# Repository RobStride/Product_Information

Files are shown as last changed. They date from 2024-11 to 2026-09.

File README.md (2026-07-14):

# RobStride 产品资料 / Product Information

北京灵足时代科技有限公司（RobStride Dynamics Co., Ltd）RS 系列一体化高性能关节模组产品资料。

- 产品规格文档：[灵足时代 RS 系列产品规格介绍（260713）](./灵足时代RS系列产品规格介绍(260713）.pdf)
- 中文资料：[产品资料](./产品资料)
- English literature: [Product Literature](./Product%20Literature)
- 官网 / Website: [www.robstride.com](https://www.robstride.com)

> 以下参数整理自 2026-07-13 版产品规格文档。额定扭矩需配合文档注明的铝制散热板条件使用；完整尺寸、性能曲线及过载曲线请查看原 PDF。

## 产品选型 / Product Selection

| 型号 Model | 产品类型 Product | 价格 Price | 额定扭矩 Rated Torque | 峰值扭矩 Peak Torque | 额定电压 Rated Voltage | 电压范围 Voltage Range | 空载转速 No-load Speed | 重量 Weight | 减速比 Ratio | 磁编码器 Encoders |
| --- | --- | ---: | ---: | ---: | ---: | ---: | ---: | ---: | ---: | ---: |
| RS00 | 14 N·m 一体化准直驱关节模组 / Integrated QDD Actuator | ¥598 | 5 N·m @ 100 rpm | 14 N·m | 48 V | 24–60 V | 315 rpm ±10% | 310 g ±3 g | 10:1 | 2 |
| RS01 | 17 N·m 一体化准直驱关节模组 / Integrated QDD Actuator | ¥599 | 7 N·m @ 100 rpm | 17 N·m | 36 V | 24–48 V | 315 rpm ±10% | 380 g ±3 g | 7.75:1 | 1 |
| RS02 | 17 N·m 一体化准直驱关节模组 / Integrated QDD Actuator | ¥699 | 7 N·m @ 100 rpm | 17 N·m | 48 V | 24–60 V | 410 rpm ±10% | 380 g ±3 g | 7.75:1 | 2 |
| RS02-IP67 | 17 N·m IP67 一体化准直驱关节模组 / IP67 Integrated QDD Actuator | ¥999 | 7 N·m @ 100 rpm | 17 N·m | 48 V | 24–60 V | 410 rpm ±10% | 490 g | 7.75:1 | 2 |
| RS03 | 60 N·m 一体化准直驱关节模组 / Integrated QDD Actuator | ¥999 | 21 N·m @ 100 rpm | 60 N·m | 48 V | 15–60 V | 195 rpm ±10% | 900 g ±20 g | 9:1 | 2 |
| RS04 | 120 N·m 一体化准直驱关节模组 / Integrated QDD Actuator | ¥1199 | 40 N·m / 35 N·m @ 50 rpm¹ | 120 N·m | 48 V | 15–60 V | 200 rpm ±10% | 1420 g ±20 g | 9:1 | 2 |
| RS05 | 5.5 N·m 一体化准直驱关节模组 / Integrated QDD Actuator | ¥499 | 1.8 N·m @ 100 rpm | 5.5 N·m | 48 V | 15–60 V | 480 rpm ±10% | 191 g | 7.75:1 | 2 |
| RS06 | 36 N·m 一体化准直驱关节模组 / Integrated QDD Actuator | ¥849 | 11 N·m @ 100 rpm | 36 N·m | 48 V | 15–60 V | 480 rpm ±10% | 621 g | 9:1 | 2 |

¹ RS04 使用 345 mm × 345 mm 铝制散热板时额定扭矩为 40 N·m；使用 220 mm × 200 mm 铝制散热板时为 35 N·m。

## 通用特性 / Common Specifications

- 驱动方式 / Drive method：FOC
- 相数 / Phases：3
- 运转方向 / Running direction：CW/CCW
- 使用温度 / Operating temperature：-20–50 ℃
- 使用湿度 / Operating humidity：5–85%
- 保存温度 / Storage temperature：-30–70 ℃
- 绝缘等级 / Insulation class：Class B
- 齿轮工艺 / Gear material：机加工钢 / Machined steel

## 使用说明书 / User Manuals

| 型号 Model | 中文说明书 | English Manual | 3D 模型 |
| --- | --- | --- | --- |
| RS00 | [RS00 使用说明书 260713](./产品资料/RS00/RS00使用说明书260713.pdf) | [RS00 User Manual](./Product%20Literature/RS00/RS00User%20Manual260713.pdf) | [RS00 STEP](./产品资料/RS00/RS00.step) |
| RS01 | [RS01 使用说明书 260713](./产品资料/RS01/RS01使用说明书260713.pdf) | [RS01 User Manual](./Product%20Literature/RS01/RS01User%20Manual260713.pdf) | [RS01 STEP](./产品资料/RS01/RS01.stp) |
| RS02 | [RS02 使用说明书 260713](./产品资料/RS02/RS02使用说明书260713.pdf) | [RS02 User Manual](./Product%20Literature/RS02/RS02User%20Manual260713.pdf) | [RS02 STEP](./产品资料/RS02/rs02.stp) |
| RS02-IP67 | [RS02-IP67 使用说明书 260713](./产品资料/RS02/RS02-IP67使用说明书260713.pdf) | [RS02-IP67 User Manual](./Product%20Literature/RS02/RS02-IP67User%20Manual260713.pdf) | [RS02-IP67 STEP](./产品资料/RS02/RS02-ip67.STEP) |
| RS03 | [RS03 使用说明书 260713](./产品资料/RS03/RS03使用说明书260713.pdf) | [RS03 User Manual](./Product%20Literature/RS03/RS03User%20Manual260713.pdf) | [RS03 STEP](./产品资料/RS03/RS03.stp) |
| RS04 | [RS04 使用说明书 260713](./产品资料/RS04/RS04使用说明书260713.pdf) | [RS04 User Manual](./Product%20Literature/RS04/RS04User%20Manual260713.pdf) | [RS04 STEP](./产品资料/RS04/RS04.stp) |
| RS05 | [RS05 使用说明书 260713](./产品资料/RS05/RS05使用说明书260713.pdf) | [RS05 User Manual](./Product%20Literature/RS05/RS05User%20Manual260713.pdf) | [RS05 STEP](./产品资料/RS05/RS05.STEP) |
| RS06 | [RS06 使用说明书 260713](./产品资料/RS06/RS06使用说明书260713.pdf) | [RS06 User Manual](./Product%20Literature/RS06/RS06User%20Manual260713.pdf) | [RS06 STEP](./产品资料/RS06/RS06-new.step) |

## 其他资料 / Additional Resources

- [CANopen 协议与配置资料](./产品资料/canopen)
- [CANopen protocol and configuration](./Product%20Literature/canopen)
- [CANHUB](./产品资料/canhub)
- [泄放模块 / Discharge Module](./产品资料/dischargeModule)
- [电源板 / Power Board](./产品资料/powerBoard)
- [OTA 升级工具与协议 / OTA Tool and Protocol](./OTA)

## 说明 / Notes

- 产品价格及规格以 2026-07-13 版规格文档为准，后续可能调整。
- RS02-IP67 的防护等级为 IP67；其他型号未在规格文档中标注 IP 防护等级。
- 中文和英文说明书的版本日期可能不同，请以对应文件内容为准。

---

# RobStride Product Information (English)

Product information for the RobStride RS Series integrated high-performance joint actuators manufactured by RobStride Dynamics Co., Ltd.

- Product specification: [RobStride RS Series Product Specifications (2026-07-13)](./灵足时代RS系列产品规格介绍(260713）.pdf)
- English literature: [Product Literature](./Product%20Literature)
- Chinese literature: [产品资料](./产品资料)
- Website: [www.robstride.com](https://www.robstride.com)
- Email: shaoyuanxin@robstride.com

> The specifications below are taken from the product specification dated July 13, 2026. The rated torque values require the aluminum heat sinks specified in the document. Refer to the original PDF for complete dimensions, performance curves, and overload curves.

## Product Selection

| Model | Product | Price | Rated Torque | Peak Torque | Rated Voltage | Voltage Range | No-load Speed | Weight | Reduction Ratio | Magnetic Encoders |
| --- | --- | ---: | ---: | ---: | ---: | ---: | ---: | ---: | ---: | ---: |
| RS00 | 14 N·m Integrated QDD Actuator | ¥598 | 5 N·m @ 100 rpm | 14 N·m | 48 V | 24–60 V | 315 rpm ±10% | 310 g ±3 g | 10:1 | 2 |
| RS01 | 17 N·m Integrated QDD Actuator | ¥599 | 7 N·m @ 100 rpm | 17 N·m | 36 V | 24–48 V | 315 rpm ±10% | 380 g ±3 g | 7.75:1 | 1 |
| RS02 | 17 N·m Integrated QDD Actuator | ¥699 | 7 N·m @ 100 rpm | 17 N·m | 48 V | 24–60 V | 410 rpm ±10% | 380 g ±3 g | 7.75:1 | 2 |
| RS02-IP67 | 17 N·m IP67 Integrated QDD Actuator | ¥999 | 7 N·m @ 100 rpm | 17 N·m | 48 V | 24–60 V | 410 rpm ±10% | 490 g | 7.75:1 | 2 |
| RS03 | 60 N·m Integrated QDD Actuator | ¥999 | 21 N·m @ 100 rpm | 60 N·m | 48 V | 15–60 V | 195 rpm ±10% | 900 g ±20 g | 9:1 | 2 |
| RS04 | 120 N·m Integrated QDD Actuator | ¥1199 | 40 N·m / 35 N·m @ 50 rpm¹ | 120 N·m | 48 V | 15–60 V | 200 rpm ±10% | 1420 g ±20 g | 9:1 | 2 |
| RS05 | 5.5 N·m Integrated QDD Actuator | ¥499 | 1.8 N·m @ 100 rpm | 5.5 N·m | 48 V | 15–60 V | 480 rpm ±10% | 191 g | 7.75:1 | 2 |
| RS06 | 36 N·m Integrated QDD Actuator | ¥849 | 11 N·m @ 100 rpm | 36 N·m | 48 V | 15–60 V | 480 rpm ±10% | 621 g | 9:1 | 2 |

¹ The RS04 rated torque is 40 N·m with a 345 mm × 345 mm aluminum heat sink, or 35 N·m with a 220 mm × 200 mm aluminum heat sink.

## Common Specifications

- Drive method: FOC
- Phases: 3
- Running direction: CW/CCW
- Operating temperature: -20–50 ℃
- Operating humidity: 5–85%
- Storage temperature: -30–70 ℃
- Insulation class: Class B
- Gear material: machined steel

## User Manuals

| Model | English Manual | Chinese Manual | 3D Model |
| --- | --- | --- | --- |
| RS00 | [RS00 User Manual](./Product%20Literature/RS00/RS00User%20Manual260713.pdf) | [RS00 Chinese Manual](./产品资料/RS00/RS00使用说明书260713.pdf) | [RS00 STEP](./Product%20Literature/RS00/RS00.step) |
| RS01 | [RS01 User Manual](./Product%20Literature/RS01/RS01User%20Manual260713.pdf) | [RS01 Chinese Manual](./产品资料/RS01/RS01使用说明书260713.pdf) | [RS01 STEP](./Product%20Literature/RS01/RS01.stp) |
| RS02 | [RS02 User Manual](./Product%20Literature/RS02/RS02User%20Manual260713.pdf) | [RS02 Chinese Manual](./产品资料/RS02/RS02使用说明书260713.pdf) | [RS02 STEP](./Product%20Literature/RS02/rs02.stp) |
| RS02-IP67 | [RS02-IP67 User Manual](./Product%20Literature/RS02/RS02-IP67User%20Manual260713.pdf) | [RS02-IP67 Chinese Manual](./产品资料/RS02/RS02-IP67使用说明书260713.pdf) | [RS02-IP67 STEP](./Product%20Literature/RS02/RS02-ip67.STEP) |
| RS03 | [RS03 User Manual](./Product%20Literature/RS03/RS03User%20Manual260713.pdf) | [RS03 Chinese Manual](./产品资料/RS03/RS03使用说明书260713.pdf) | [RS03 STEP](./Product%20Literature/RS03/RS03.stp) |
| RS04 | [RS04 User Manual](./Product%20Literature/RS04/RS04User%20Manual260713.pdf) | [RS04 Chinese Manual](./产品资料/RS04/RS04使用说明书260713.pdf) | [RS04 STEP](./Product%20Literature/RS04/RS04.stp) |
| RS05 | [RS05 User Manual](./Product%20Literature/RS05/RS05User%20Manual260713.pdf) | [RS05 Chinese Manual](./产品资料/RS05/RS05使用说明书260713.pdf) | [RS05 STEP](./Product%20Literature/RS05/RS05.STEP) |
| RS06 | [RS06 User Manual](./Product%20Literature/RS06/RS06User%20Manual260713.pdf) | [RS06 Chinese Manual](./产品资料/RS06/RS06使用说明书260713.pdf) | [RS06 STEP](./Product%20Literature/RS06/RS06-new.step) |

## Additional Resources

- [CANopen protocol and configuration](./Product%20Literature/canopen)
- [CANHUB](./Product%20Literature/canhub)
- [Discharge Module](./Product%20Literature/dischargeModule)
- [Power Board](./Product%20Literature/powerBoard)
- [OTA tool and protocol](./OTA)

## Notes

- Prices and specifications are based on the product specification dated July 13, 2026, and may change in future revisions.
- RS02-IP67 is rated IP67. No IP rating is specified for the other models in the source document.
- Chinese and English manuals may have different revision dates. Refer to the contents of the relevant file.

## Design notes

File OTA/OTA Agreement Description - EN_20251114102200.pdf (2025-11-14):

# OTA Upgrade Agreement Description

## Frame type description

1、Get Device ID (Communication Type 0); Get the device ID and 64-bit MCU unique

identifier. Data

field | 29-bitID | 8Byte data field
Size | Bit28~bit24 | bit23~8 | bit7~0 | Byte0~Byte7
Description | 0 | bit15~8:identifies host CAN_ID | target motor CAN_ID | 0

Reply frame ：

Data field | 29-bitID | 8Byte data field
Size | Bit28~bit24 | bit23~8 | bit7~0 | Byte0~Byte7
Description | 0 | target motor CAN_ID | 0XFE | 64-bit MCU unique identifier

2、Upgrate the stsrtup frame

Data field | 29-bitID | 8Byte data field
Size | Bit28~b it24 | bit23~8 | bit7~0 | Byte0~Byte7
Description | 11 | bit15~8:identifies host CAN_ID | Target motor CAN_ID | 64-bitMCUuniqueidentifier

Reply frame

Data field | 29-bitID | 8Byte data field
Size | Bit28~bit24 | bit23~8 | bit7~0 | Byte0~Byte7

Description 11

Bit23~16:
0x00: Sent successfully
0x0F：Send failed
bit15~8:Target motorCAN_ID
Host CAN_ID | 0

3、bin file parsing, upgrade information frames

Data field | 29-bitID | 8Byte data field
Size | Bit28 ~bit2 4 | bit23~8 | bit7~0 | Byte0~Byte7
Description | 12 | bit15~8:identifies host CAN_ID | Target motor CAN_ID | Byte0~Byte3 Data packet bytes binsize Byte4~Byte7 Data packet bytes PackNumber Least byte first

Reply frame

Data field | 29-bitID | 8Byte data field
Size | Bit28~bit24 | bit23~8 | bit7~0 | Byte0~Byte7
Description | 12 | Bit23~16: 0x00: Sent successfully 0x0F：Send failed bit15~8:Target motorCAN_ID | host CAN_ID | 0

4、Upgrade Frame

4.1 process frame

Data
field
29-bitID | 8Byte data field

Size | Bit28 ~bit2 4 | bit23~8 | bit7~0 | Byte0~Byte7
Description | 13 | bit15~8:升级包当前位置 | Target motor CAN_ID | Data packet bytes

Reply frame

Data field | 29-bitID | 8Byte data field
Size | Bit28~bit24 | bit23~8 | bit7~0 | Byte0~Byte7
Description | 11 | Bit23~16: 0x00: Sent successfully 0x0F：Send failed bit15~8:Target motorCAN_ID | host CAN_ID | 0

4.2 End frame

29 位 ID | 8Byte data field
Bit28~bit24 | bit23~8 | bit7~0 | Byte0~Byte7
14 | 0 | Target motor CAN_ID | Byte0~Byte3 PackNumber

Reply frame

Data field | 29-bitID | 8Byte data field
Size | Bit28~bit24 | bit23~8 | bit7~0 | Byte0~Byte7
Description | 14 | Bit23~16: 0x00: Sent successfully 0x0F：Send failed bit15~8:Target motorCAN_ID | host CAN_ID | Sent successfully： Meaningless Send failed： Byte0~Byte3 Current upgrade location

## Detailed process description (based on QT)

The parameters are defined below. enum canComMode{

CANCOM_ANNOUNCE_DEVID = 0,//Notification Device ID CANCOM_MOTOR_CTRL, //MOTOR-Motor control CANCOM_MOTOR_FEEDBACK, //MOTOR-Motor feedback
CANCOM_MOTOR_IN, | //MOTOR-Enter motor mode
CANCOM_MOTOR_RESET, | //MOTOR-Reset mode
CANCOM_MOTOR_CALI, | //MOTOR-High-speed encoder calibration
CANCOM_MOTOR_ZERO, | //MOTOR-Set mechanical zero position
CANCOM_MOTOR_ID, | //MOTOR-Set ID
CANCOM_PARA_WRITE, | //Parameters - Write
CANCOM_PARA_READ, | //Parameters - Read
CANCOM_PARA_UPDATE, | //Parameters - Update Upload
CANCOM_OTA_START, | //OTA-start up
CANCOM_OTA_INFO, | //OTA-Upgrade file description
CANCOM_OTA_ING, | //OTA-Upgrading
CANCOM_OTA_END, | //OTA-Upgrade complete
CANCOM_CALI_ING, | //Encoder calibration
CANCOM_CALI_RST, | //Encoder calibration results
CANCOM_SDO_READ, | //sdo
CANCOM_SDO_WRITE, | //sdo
CANCOM_PARA_STR_INFO, | //Parameter - String Information
CANCOM_MOTOR_BRAKE, | //MOTOR-Enter braking mode
CANCOM_FAULT_WARN, | //Fault and warning messages
CANCOM_MODE_TOTAL, };

struct exCanIdInfo{
quint32 id:8;
quint32 data:16;
enum canComMode mode:5;
quint32 res:3;
};

struct canPack{
Struct exCanIdInfo exId;
quint8 len;
quint8 data[8];
};

struct canPack pack;

memset(&pack,0,sizeof (struct canPack)); pack.len = 8;
pack.exId.id = devCanId;//Assignment motor canid quint32 addr;
QString FilePath;
QByteArray BinData;

The specific process is as follows. 1、Identify the bin file path and read file information. void MainWindow::on_pushButtonOpenFile_clicked()

{
BinData.clear();//Clear
FilePath = QFileDialog::getOpenFileName(this,tr("Open Binary File"), ".", tr("Binary File(*.bin *.hex)"));

if(FilePath.length())
{
QFile file(FilePath);
if(file.open(QIODevice::ReadOnly))
{
BinData = file.readAll();//read file file.close();
}
}
}
2、Send upgrade start frame
pack.exId.data = 0xFD; //host id
pack.exId.mode = CANCOM_OTA_START; memcpy(&(pack.data[0]),&(mcuBuf.id[mcuBuf.usePos]),8);//The data bits are mcuid, obtained through type 0. txdPack(&pack);

break;
If a feedback frame is received, proceed to the next step. 4、Send an upgrade information frame containing packet size information. binSize = BinData.size();

if(binSize==0)
{
//This path indicates that the file was not recognized. }

else if(binSize > 0X80000)
{
//This path indicates that the identified file is too large and is not the target file.

}
else
{
PackNumber = binSize / 8;
if(binSize % 8)
{
PackNumber += 1;
}
PackCnt = 0;
memcpy(&(pack.data[0]),&binSize,4); memcpy(&(pack.data[4]),&PackNumber,4); pack.exId.data = 0xFD; //主机 id pack.exId.mode = CANCOM_OTA_INFO; txdPack(&pack);
}
break;
If feedback is received, you can proceed to the next step. 5. Send frames in a loop, sending one frame and receiving feedback for each frame sent; only

send the next frame after receiving feedback. 6. First send a process frame

pack.exId.data = PackCnt;
addr = PackCnt*8;
for(uint8_t i=0;i<8;i++,addr++)
{
if(addr<binSize) pack.data[i]=BinData[PackCnt*8+i];
else | pack.data[i]=0XFF;
}
txdPack(&pack);
Once feedback is received and the interrupt is received, the function below can be looped. if(rxFrame.exId.data == devCanId) //If the error position in the feedback frame is set to 0, it indicates successful transmission, and the sequence number is incremented by 1. {

PackCnt++;
}
else if(rxFrame.exId.data == ((quint16)devCanId|0X0F00)) //If the error bit in the feedback frame is 0x0F, it indicates that the transmission failed. The frame should be retransmitted, and the interruption should be resumed. {

memcpy(&PackCnt,rxFrame.data,2);
}
if(PackCnt >= PackNumber) //End frame, this frame indicates that the upgrade is complete. {

pack.exId.data = 0;

pack.exId.mode = CANCOM_OTA_END; memcpy(&(pack.data[0]),&PackNumber,4); txdPack(&pack);
break;
}
else //process frame
{
pack.exId.data = PackCnt;
addr = PackCnt*8;
for(uint8_t i=0;i<8;i++,addr++)
{
if(addr<binSize) pack.data[i]=BinData[PackCnt*8+i];
else | pack.data[i]=0XFF;
}
txdPack(&pack);
QThread::msleep(1); //Delay 1ms
break;
}
An upgrade delay check can be added. If no feedback frame is detected for an extended period, it indicates a communication problem, and the motor can be powered on again for another upgrade.

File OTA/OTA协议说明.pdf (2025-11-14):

## OTA 升级协议说明

帧类型说明

1、获取设备 ID （通信类型 0） ；获取设备的 ID 和 64 位 MCU 唯一标识符

数据域 | 29 位 ID | 8Byte 数据区
大小 | Bit28~bit24 | bit23~8 | bit7~0 | Byte0~Byte7
描述 | 0 | bit15~8:用来标识主机 CAN_ID | 目标电机 CAN_ID | 0

应答帧：

数据域 | 29 位 ID | 8Byte 数据区
大小 | Bit28~bit24 | bit23~8 | bit7~0 | Byte0~Byte7
描述 | 0 | 目标电机 CAN_ID | 0XFE | 64 位 MCU 唯一标识符

2、升级启动帧

数 据 域 | 29 位 ID | 8Byte 数据区
大 小 | Bit28~bit24 | bit23~8 | bit7~0 | Byte0~Byte7
描 述 | 11 | bit15~8:用来标识主机 CAN_ID | 目标电机 CAN_ID | 64 位 MCU 唯一标识符

反馈帧

数据域 | 29 位 ID | 8Byte 数据区
大小 | Bit28~bit24 | bit23~8 | bit7~0 | Byte0~Byte7
描述 | 11 | Bit23~16: 0x00: 发送成功 0xF0：发送失败 bit15~8:目标电机 CAN_ID | 主机 CAN_ID | 0

3、bin 文件解析，升级信息帧

数 据 域 | 29 位 ID | 8Byte 数据区
大 小 | Bit28~bit24 | bit23~8 | bit7~0 | Byte0~Byte7
描 述 | 12 | bit15~8:用来标识主机 CAN_ID | 目标电机 CAN_ID | Byte0~Byte3 数据包字节数 binsize Byte4~Byte7 数 据 包 字 数 PackNumber 低字节在前

反馈帧

数据域 | 29 位 ID | 8Byte 数据区
大小 | Bit28~bit24 | bit23~8 | bit7~0 | Byte0~Byte7
描述 | 12 | Bit23~16: 0x00: 发送成功 0xF0：发送失败 bit15~8:目标电机 CAN_ID | 主机 CAN_ID | 0

4、升级帧

4.1 过程帧

数 据 域 | 29 位 ID | 8Byte 数据区
大 小 | Bit28~bit24 | bit23~8 | bit7~0 | Byte0~Byte7
描 述 | 13 | bit15~8:升级包当前位置 | 目标电机 CAN_ID | 数据包数据

反馈帧

数据域 | 29 位 ID | 8Byte 数据区
大小 | Bit28~bit24 | bit23~8 | bit7~0 | Byte0~Byte7
描述 | 11 | Bit23~16: 0x00: 发送成功 0xF0：发送失败 bit15~8:目标电机 CAN_ID | 主机 CAN_ID | 0

4.2 结束帧

29 位 ID | 8Byte 数据区
Bit28~bit24 | bit23~8 | bit7~0 | Byte0~Byte7
14 | bit15~8:升级包当前位置 | 目标电机 CAN_ID | 数据包数据

反馈帧

数据域 | 29 位 ID | 8Byte 数据区
大小 | Bit28~bit24 | bit23~8 | bit7~0 | Byte0~Byte7
描述 | 14 | Bit23~16: 0x00: 发送成功 0xF0：发送失败 bit15~8:目标电机 CAN_ID | 主机 CAN_ID | Byte0~Byte1 升 级 包 当 前位置

详细流程说明（基于 QT）

下方为定义参数

enum canComMode{
CANCOM_ANNOUNCE_DEVID = 0,//通告设备 ID CANCOM_MOTOR_CTRL, //MOTOR-电机控制 CANCOM_MOTOR_FEEDBACK, //MOTOR-电机反馈
CANCOM_MOTOR_IN, | //MOTOR-进入电机模式
CANCOM_MOTOR_RESET, | //MOTOR-复位模式
CANCOM_MOTOR_CALI, | //MOTOR-高速编码器标定
CANCOM_MOTOR_ZERO, | //MOTOR-设置机械零位
CANCOM_MOTOR_ID, | //MOTOR-设置 ID
CANCOM_PARA_WRITE, | //参数-写入
CANCOM_PARA_READ, | //参数-读取
CANCOM_PARA_UPDATE, | //参数-更新上传

CANCOM_OTA_START, | //OTA-启动
CANCOM_OTA_INFO, | //OTA-升级文件描述
CANCOM_OTA_ING, | //OTA-升级中
CANCOM_OTA_END, | //OTA-升级完成
CANCOM_CALI_ING, | //编码器标定中
CANCOM_CALI_RST, | //编码器标定结果
CANCOM_SDO_READ, | //sdo
CANCOM_SDO_WRITE, | //sdo
CANCOM_PARA_STR_INFO, | //参数-字符串信息
CANCOM_MOTOR_BRAKE, | //MOTOR-进入刹车模式
CANCOM_FAULT_WARN, | //故障和警告信息
CANCOM_MODE_TOTAL, };

struct exCanIdInfo{
quint32 id:8;
quint32 data:16;
enum canComMode mode:5;
quint32 res:3;
};

struct canPack{
Struct exCanIdInfo exId;
quint8 len;
quint8 data[8];
};

struct canPack pack;
memset(&pack,0,sizeof (struct canPack)); pack.len = 8;
pack.exId.id = devCanId;//赋值电机 canid quint32 addr;
QString FilePath;
QByteArray BinData;

下面为具体流程

1、识别 bin 文件路径，读取文件信息
void MainWindow::on_pushButtonOpenFile_clicked()
{
BinData.clear();//清空
FilePath = QFileDialog::getOpenFileName(this,tr("Open Binary File"), ".", tr("Binary File(*.bin *.hex)"));

if(FilePath.length())
{
QFile file(FilePath);
if(file.open(QIODevice::ReadOnly))
{
BinData = file.readAll();//read file file.close();
}
}
}
2、发送升级启动帧
pack.exId.data = 0xFD; //主机 id
pack.exId.mode = CANCOM_OTA_START; memcpy(&(pack.data[0]),&(mcuBuf.id[mcuBuf.usePos]),8);//数据位是 mcuid，通过类型 0
获得
txdPack(&pack);
break;
如接收到反馈帧可继续下一步

3、发送升级信息帧，包含包大小的信息
binSize = BinData.size();
if(binSize==0)
{
//该路径表示未识别到文件
}
else if(binSize > 0X80000)
{
//该路径表示识别的文件大小过大，非目标文件
}
else
{
PackNumber = binSize / 8;
if(binSize % 8)
{
PackNumber += 1;
}
PackCnt = 0;
memcpy(&(pack.data[0]),&binSize,4); memcpy(&(pack.data[4]),&PackNumber,4); pack.exId.data = 0xFD; //主机 id pack.exId.mode = CANCOM_OTA_INFO; txdPack(&pack);
}
break;

如接收到反馈可继续下一步

5、循环发送，发送一帧反馈一帧，接收到反馈后再发送下一帧 先发送一个过程帧
pack.exId.data = PackCnt;
addr = PackCnt*8;
for(uint8_t i=0;i<8;i++,addr++)
{
if(addr<binSize) pack.data[i]=BinData[PackCnt*8+i];
else | pack.data[i]=0XFF;
}
txdPack(&pack);
等到反馈，接收中断后就可以循环下方函数
if(rxFrame.exId.data == devCanId) //反馈帧错误位置 0，表示发送成功，顺序号加 1 {
PackCnt++;
}
else if(rxFrame.exId.data == ((quint16)devCanId|0X0F00)) //反馈帧错误位为 0x0F，表示发送
失败，重新发送该帧，断点续接
{
memcpy(&PackCnt,rxFrame.data,2);
}
if(PackCnt >= PackNumber) //结束帧，该帧表示升级完成 {
pack.exId.data = 0;
pack.exId.mode = CANCOM_OTA_END; memcpy(&(pack.data[0]),&PackNumber,4); txdPack(&pack);
break;
}
else //过程帧
{
pack.exId.data = PackCnt;
addr = PackCnt*8;
for(uint8_t i=0;i<8;i++,addr++)
{
if(addr<binSize) pack.data[i]=BinData[PackCnt*8+i];
else | pack.data[i]=0XFF;
}
txdPack(&pack);
QThread::msleep(1); //延时 1ms
break;
}
可以加一个升级延时判定，如果发现长时间没有反馈帧，那就表示通信出现问题，可以电机

重新上电再次升级

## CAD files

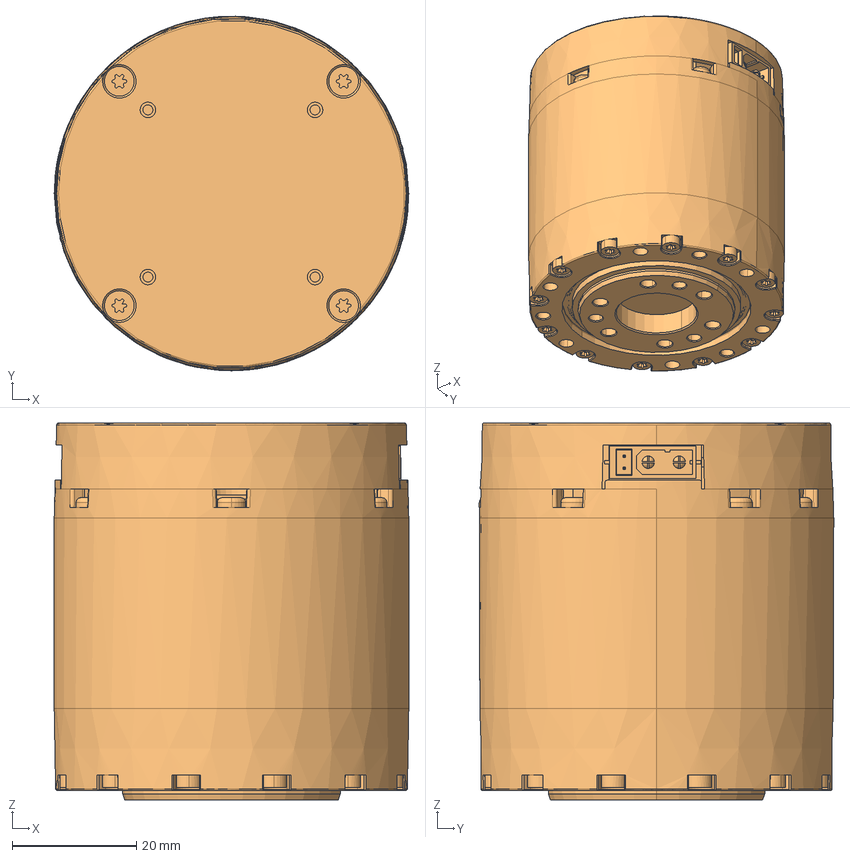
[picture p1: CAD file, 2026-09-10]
Product Literature/10P/RS10.stp
57.0 x 57.0 x 60.6 mm

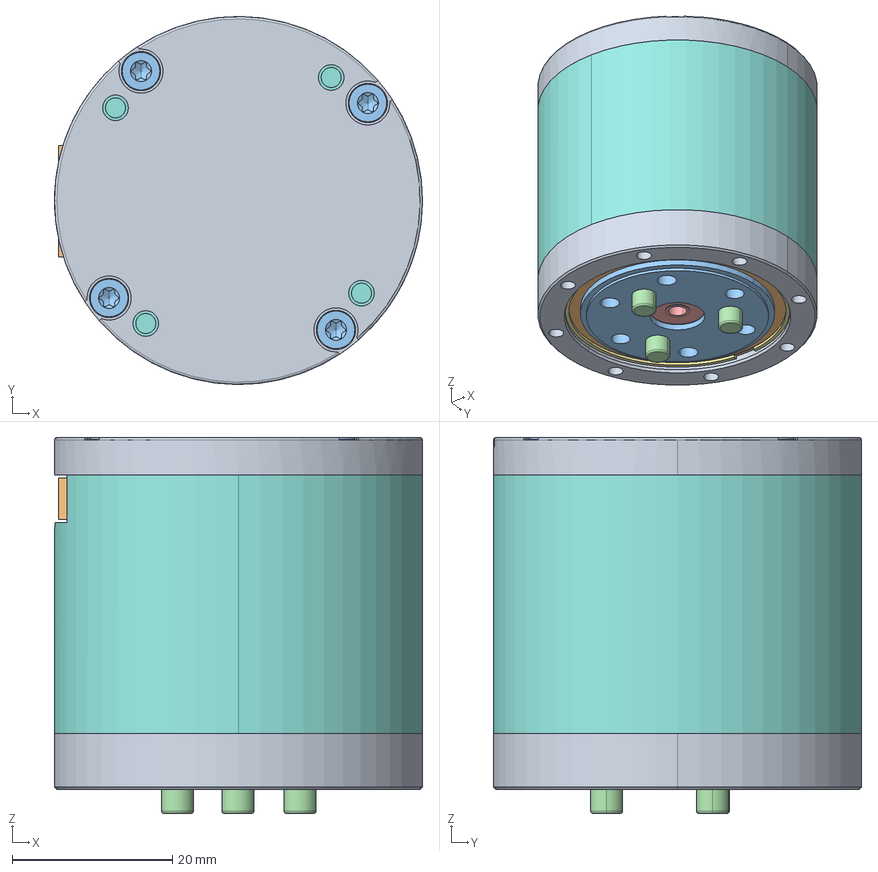
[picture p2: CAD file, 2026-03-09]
Product Literature/EL05/el05.stp
46.0 x 46.0 x 47.0 mm
PRT0001_1
LUOSI_1_1 x 4

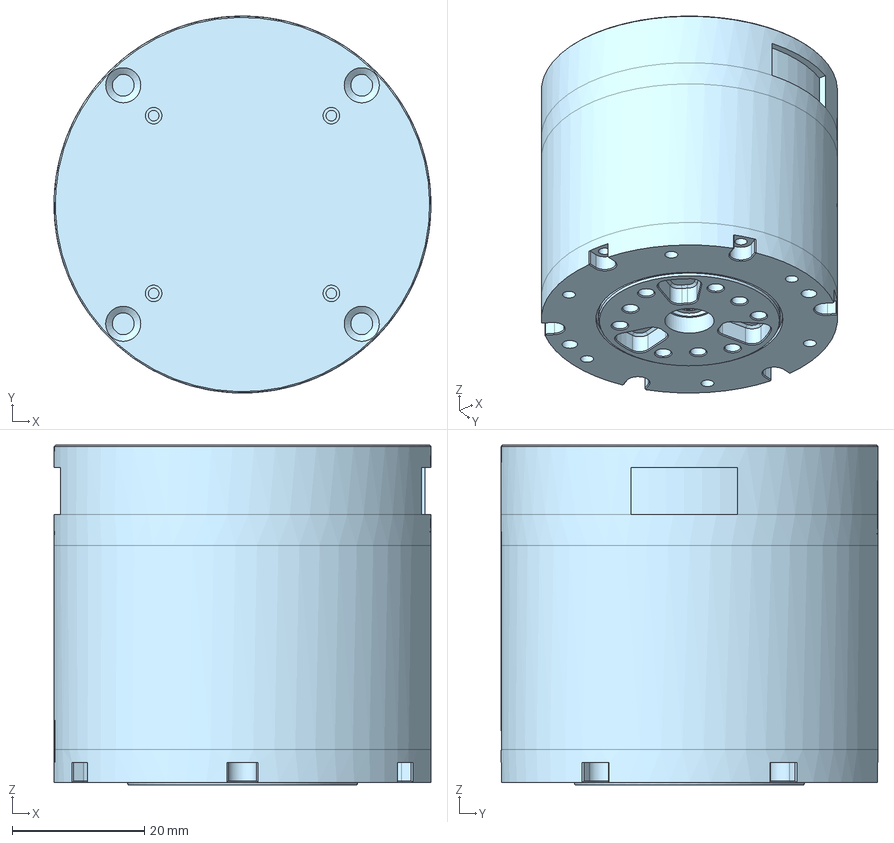
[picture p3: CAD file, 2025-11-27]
Product Literature/RS00/RS00.step
57.0 x 57.0 x 51.4 mm

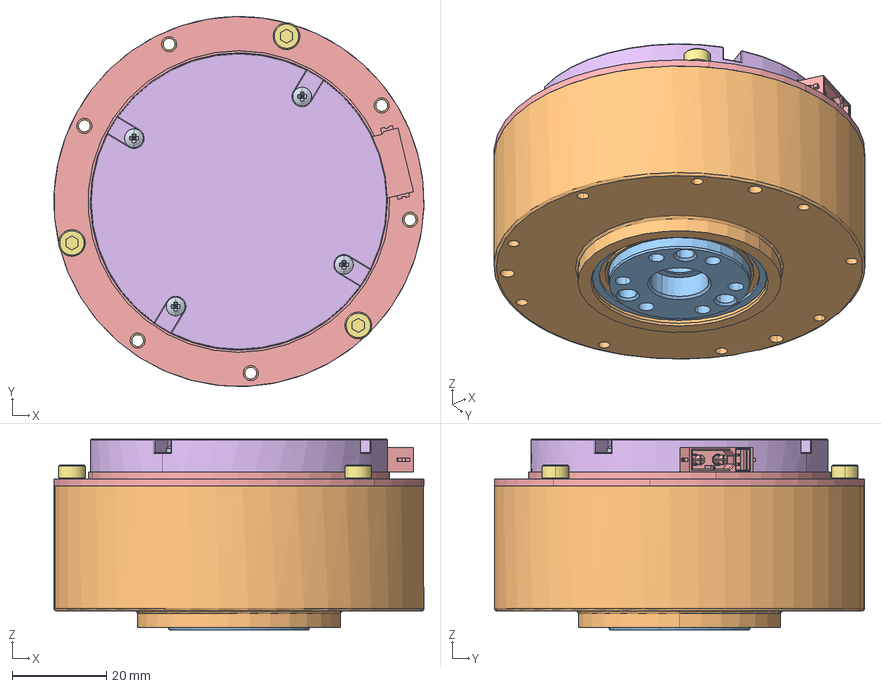
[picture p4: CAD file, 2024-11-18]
Product Literature/RS01/RS01.stp
78.4 x 78.5 x 40.5 mm
1_1_06_EB673-510_1
1_1_02_EB671-502_1
1_1_27_SK671-506_ASM_1_ASM
1_1_31_QT-904_1
1_1_06_EB673-502_1
1_2_05_QT-170_1 x 4
DIANJIBAN
DUANZI_1_3_1_1_1_1_1_1_1

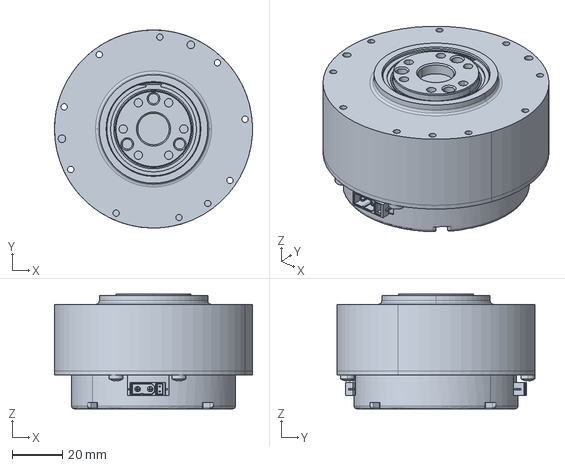
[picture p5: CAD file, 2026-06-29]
Product Literature/RS02/rs02.stp
78.5 x 78.5 x 45.4 mm

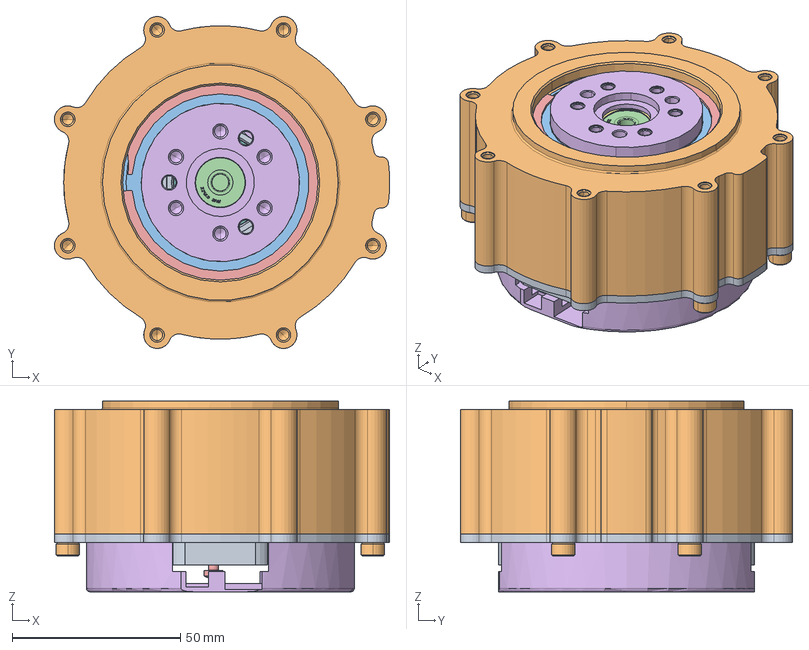
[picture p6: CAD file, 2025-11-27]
Product Literature/RS03/RS03.stp
99.5 x 98.5 x 56.6 mm
1_1_06_EB903-537_AF0_1
1_1_27_SK901-517_ASM_1_ASM
1_1_06_EB903-536_ASM_1_ASM
1_1_02_EB901-558_1
1_2_06_000004_AF0_1
1_1_31_QT-942_1
1_1_11_MG80-S003_1 x 2
1_1_06_EB903-538_1

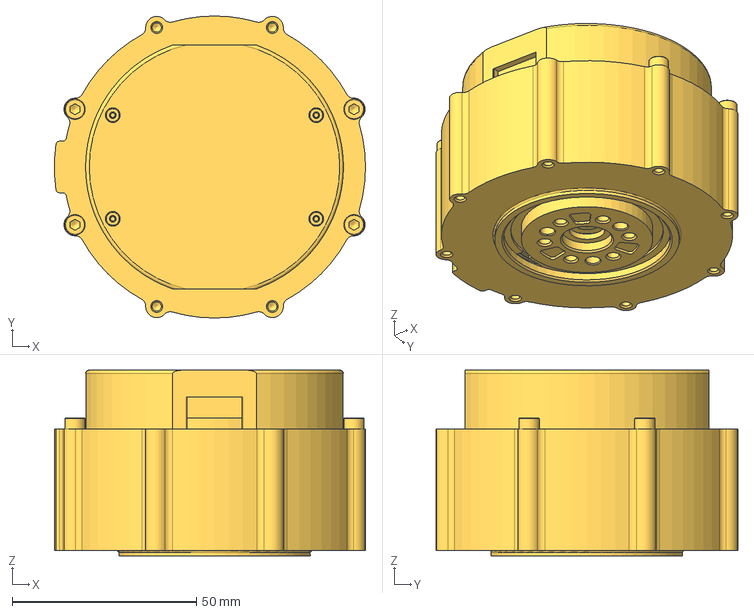
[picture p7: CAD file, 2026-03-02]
Product Literature/RS06/RS06-new.step
84.5 x 82.0 x 50.5 mm

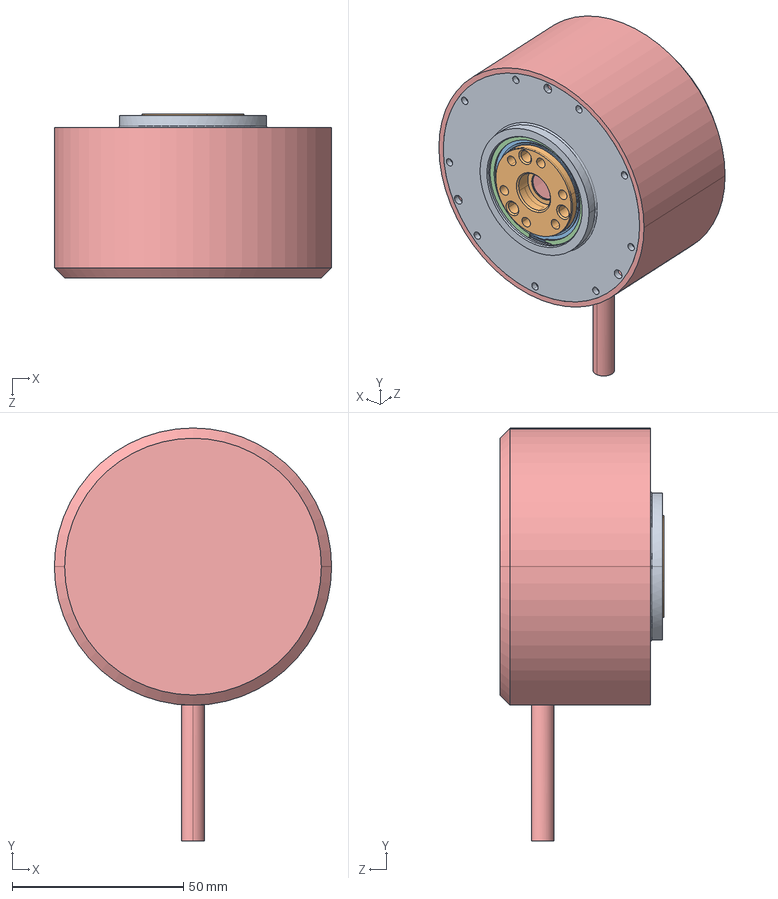
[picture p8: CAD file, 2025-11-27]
Product Literature/RS02/RS02-ip67.STEP
81.0 x 120.7 x 48.0 mm
1_1_06_EB673-516_1.stp.STEP
1_1_02_EB671-502_1.stp.STEP
1_2_04_670601_1.stp.STEP
1_2_06_000392_1.stp.STEP
零件15^RS02-ip67

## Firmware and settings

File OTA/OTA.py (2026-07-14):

import can
import time
import os


# ===================== 用户配置 =====================
UPGRADE_BIN_PATH = r"/home/liu/Downloads/rs00_0.0.3.22.bin"

TARGET_MOTOR_ID = 0x03
HOST_ID = 0xFD

CAN_CHANNEL = "can0"
CAN_BITRATE = 1000000

TIMEOUT = 2.0
RETRY_CNT = 3


# ===================== 协议枚举 =====================
CANCOM_ANNOUNCE_DEVID = 0
CANCOM_OTA_START = 11
CANCOM_OTA_INFO = 12
CANCOM_OTA_ING = 13
CANCOM_OTA_END = 14

FEEDBACK_SUCCESS = 0x00
FEEDBACK_FAILED = 0xF0


class MotorOTA:

    def __init__(self):
        self.bus = None
        self.bin_data = b""
        self.bin_size = 0
        self.pack_number = 0
        self.pack_cnt = 0
        self.mcu_uid = None

    # ===================== 构造29位ID =====================
    def build_id(self, mode, data, dev_id):
        return (((mode & 0x1F) << 24)
                | ((data & 0xFFFF) << 8)
                | (dev_id & 0xFF)) & 0x1FFFFFFF

    # ===================== 解析29位ID =====================
    def parse_id(self, can_id):
        can_id &= 0x1FFFFFFF
        mode = (can_id >> 24) & 0x1F
        data = (can_id >> 8) & 0xFFFF
        dev_id = can_id & 0xFF
        return mode, data, dev_id

    # ===================== 初始化CAN =====================
    def init_can(self):
        self.bus = can.interface.Bus(
            channel=CAN_CHANNEL,
            interface="socketcan",
            bitrate=CAN_BITRATE
        )
        print("✅ CAN 初始化成功")

    # ===================== 发送并等待ACK =====================
    def send_and_wait_ack(self, mode, data, payload):

        tx_id = self.build_id(mode, data, TARGET_MOTOR_ID)

        msg = can.Message(
            arbitration_id=tx_id,
            data=payload,
            is_extended_id=True
        )

        for retry in range(RETRY_CNT):

            print(f"TX: {hex(tx_id)}")

            self.bus.send(msg)

            start = time.time()
            while time.time() - start < TIMEOUT:

                rx = self.bus.recv(timeout=0.1)
                if not rx or not rx.is_extended_id:
                    continue

                rx_mode, rx_data, rx_id = self.parse_id(rx.arbitration_id)

                # 必须是同模式
                if rx_mode != mode:
                    continue

                # 必须回给主机
                if rx_id != HOST_ID:
                    continue

                result = (rx_data >> 8) & 0xFF
                motor_id = rx_data & 0xFF

                if motor_id != TARGET_MOTOR_ID:
                    continue

                if result == FEEDBACK_SUCCESS:
                    return True, rx

                if result == FEEDBACK_FAILED:
                    return False, rx

            print("⚠ 超时重试...")
            time.sleep(0.05)

        return False, None

    # ===================== 获取设备ID =====================
    def get_device_id(self):

        print("📡 获取设备ID...")

        tx_id = self.build_id(
            CANCOM_ANNOUNCE_DEVID,
            HOST_ID,          # ❗ 这里不再 <<8
            TARGET_MOTOR_ID
        )

        msg = can.Message(
            arbitration_id=tx_id,
            data=[0] * 8,
            is_extended_id=True
        )

        self.bus.send(msg)

        start = time.time()
        while time.time() - start < TIMEOUT:

            rx = self.bus.recv(timeout=0.1)
            if not rx:
                continue

            mode, data, dev_id = self.parse_id(rx.arbitration_id)

            if mode != CANCOM_ANNOUNCE_DEVID:
                continue

            if dev_id != 0xFE:
                continue

            self.mcu_uid = rx.data
            print("✅ MCU UID:", self.mcu_uid.hex())
            return True

        print("❌ 获取设备ID失败")
        return False

    # ===================== 读取BIN =====================
    def read_bin(self, path):

        if not os.path.exists(path):
            print("❌ BIN文件不存在")
            return False

        with open(path, "rb") as f:
            self.bin_data = f.read()

        self.bin_size = len(self.bin_data)

        if self.bin_size == 0 or self.bin_size > 0x80000:
            print("❌ BIN非法")
            return False

        self.pack_number = (self.bin_size + 7) // 8

        print(f"BIN大小: {self.bin_size}")
        print(f"总包数: {self.pack_number}")

        return True

    # ===================== OTA流程 =====================
    def start_upgrade(self, path):

        self.init_can()

        if not self.read_bin(path):
            return

        if not self.get_device_id():
            return

        # ===== START =====
        ok, _ = self.send_and_wait_ack(
            CANCOM_OTA_START,
            HOST_ID,
            list(self.mcu_uid)
        )
        if not ok:
            print("❌ START失败")
            return

        # ===== INFO =====
        payload = list(self.bin_size.to_bytes(4, "little"))
        payload += list(self.pack_number.to_bytes(4, "little"))

        ok, _ = self.send_and_wait_ack(
            CANCOM_OTA_INFO,
            HOST_ID,
            payload
        )
        if not ok:
            print("❌ INFO失败")
            return

        # ===== ING =====
        self.pack_cnt = 0

        while self.pack_cnt < self.pack_number:

            start_index = self.pack_cnt * 8
            chunk = self.bin_data[start_index:start_index+8]
            payload = list(chunk) + [0xFF]*(8-len(chunk))

            ok, rx = self.send_and_wait_ack(
                CANCOM_OTA_ING,
                self.pack_cnt,
                payload
            )

            if ok:
                self.pack_cnt += 1
                if self.pack_cnt % 100 == 0:
                    print(f"进度: {self.pack_cnt}/{self.pack_number}")
            else:
                if rx:
                    resend_cnt = int.from_bytes(rx.data[0:2], "little")
                    print("🔁 断点续传:", resend_cnt)
                    self.pack_cnt = resend_cnt
                else:
                    print("❌ ING失败")
                    return

        # ===== END =====
        payload = list(self.pack_number.to_bytes(4, "little")) + [0]*4

        ok, _ = self.send_and_wait_ack(
            CANCOM_OTA_END,
            0,
            payload
        )

        if ok:
            print("🎉 OTA升级完成")
        else:
            print("❌ END失败")


# ===================== 主程序 =====================
if __name__ == "__main__":
    ota = MotorOTA()
    ota.start_upgrade(UPGRADE_BIN_PATH)

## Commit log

2024-11-18 产品资料提交
    产品资料提交
    [RS01.stp, RS02.STEP, RS03.stp]
2024-11-18 Product Literature
    Product Literature
    [RS01.stp, RS02.STEP, RS03.stp]
2025-02-27 update
    update
    [RS01.stp, RS02.STEP, RS03.stp]
2025-06-26 Create 灵足时代产品规格介绍 RobStride Product Specification Document.pdf
2025-09-30 feat: add yourfile.ext 到 docs 目录
2025-11-12 add EL05
    [EL05.stp]
2025-11-27 update step
    [RS00.step, RS01.stp, RS02-ip67.STEP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]
2026-03-02 add canhub dischargemodule powerboard
    [RS06-new.step]
2026-03-10 add en-powerboard and en-discharge
2026-06-05 update powerboard
2026-06-29 update rs02-step
    [RS02.step, rs02.stp]
